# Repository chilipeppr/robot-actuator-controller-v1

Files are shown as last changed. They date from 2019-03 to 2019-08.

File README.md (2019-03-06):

# robot-actuator-controller-v1
This is a controller for the WE-R2.4 robot on Thingiverse.

It has an ESP32 at the heart of the controller to enable control of the actuator via Wifi or Bluetooth. There is a DC to DC converter to step down the 24v driving the DRV8825 stepper motor driver to 5V for powering the ESP32. The DRV8825 has all ports connected into the ESP32 to send step and direction pulses for control of the stepper motor.

There is also a WS2812 LED connected for indicating status of the controller.

A switch has been added for when you're using the USB port for programming the ESP32. You need to switch off the 5V from the DC to DC converter to connect USB from your computer.

The wrist cap has been extended from Jeff Kerr's original design to fit this larger board.

# Eagle Board and Schematic

The .brd and .sch files are Eagle board and schematic files. You can download Eagle for free to view or edit the boards or just use the .zip file in the "pcb fabricator" folder to send to your board house like JLCPCB where it only costs $2 to get your boards made.

# ESP32 Firmware

You need to upload the firmware in this repo to your ESP32 using esptool.py which is available on the Espressif website. There's also a video on http://chilipeppr.com/esp32 on how to use the workspace. This video shows you how to upload the firmware and use the workspace to upload code.

To program your board with this firmware use the command on Windows:
esptool.py --port COM5 write_flash 0x1000 bootloader.bin 0x10000 NodeMCU.bin 0x8000 partitions.bin

You need to install esptool.py via Python's package manager or from downloading direct from Espressif's website.

An alternate path is to use the esp32tool.zip I provide in the workspace and swap out the NodeMCU.bin file in this repo to the one in that zip file. Then install. You do need 3 .bin files to program the firmware. 2 of them are standard (bootloader.bina nd partitions.bin), but the NodeMCU.bin is the new file you'd have to swap in.

This firmware is configured for 230,400 baud, so don't forget to change to that value in ChiliPeppr when you connect to the board. If you try the default 115,200 it will fail.

# CAD Design Fusion 360

The CAD design of the extended wrist cap with the electronics inside is available at https://gallery.autodesk.com/fusion360/projects/robot-arm-esp32-drv8825-actuator-controller

# How to Upload the Lua Code

The ChiliPeppr ESP32 for Lua Workspace was used to program the board and is available at http://chilipeppr.com/esp32

Video on how to use the ESP32 for Lua workspace to upload firmware and Lua code on your ESP32. https://www.youtube.com/watch?v=njAeHfoVIoY

# Thingiverse

Jeff Kerr's (LoboCNC) original 3D printed robot arm design is on Thingiverse at https://www.thingiverse.com/thing:3327968/

# PCB Components

ESP32 Wemos $8 (Many ESP32 devices are cheaper, but this is the smallest size broadly available to fit inside the small actuators)
https://www.aliexpress.com/item/ESP32-wemos-ESP32-WiFi-Modules-Bluetooth-Dual-ESP-32-ESP-32S-ESP8266/32815190965.html

DRV8825 Stepper Board $0.95
https://www.aliexpress.com/item/5pcs-lot-3D-Printer-Stepstick-Drv8825-Stepper-Motor-Driver-Reprap-4-PCB-Board-Free-shipping-replace/32514641632.html

DC to DC Converter $0.90 (Pick the 5V version, not 3.3V)
https://www.aliexpress.com/item/DC-DC-Power-Supply-Module-Step-Down-3A-output-24V-12V-to-5V-3-3V-Buck/32904709711.html

WS2812B LED $0.15 per (Choose white and WS2812B)
https://www.aliexpress.com/item/10-1000pcs-4-Pin-WS2812B-WS2812-LED-Chip-Heatsink-5V-5050-RGB-WS2811-IC-Built-in/32634454437.html

Slide Switch $0.29 for 20 pieces
https://www.aliexpress.com/item/20Pcs-Interruptor-on-off-mini-Slide-Switch-SS12D00-SS12D00G3-3pin-1P2T-2-Position-High-quality-toggle/32964400942.html

Screw Terminal
https://www.aliexpress.com/item/20-pcs-2-Pin-Screw-blue-green-PCB-Terminal-Block-Connector-5mm-Pitch/32814618602.html

26AWG Silicone Ultra Flexible Wire for 24v (Use 2 of the 4 wires)
https://www.aliexpress.com/item/2metre-26AWG-28AWG-30AWG-Silicone-Wire-Ultra-Flexiable-Test-Line-3P-4P-6P-0-08mm-Tinned/32870367030.html

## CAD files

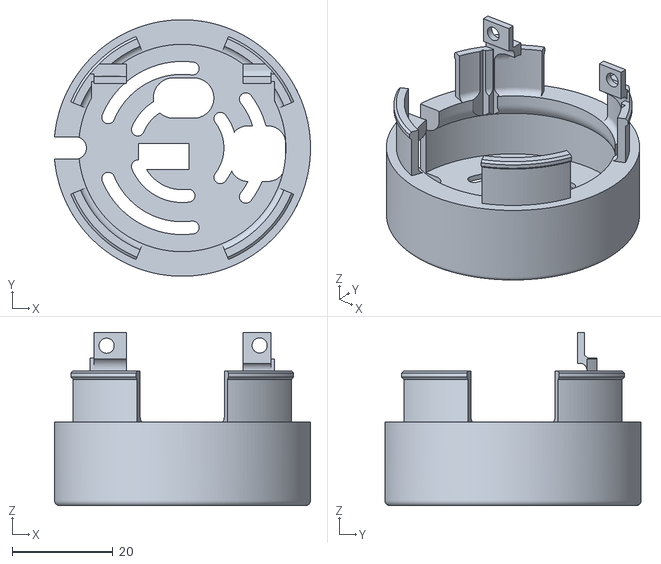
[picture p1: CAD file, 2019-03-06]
stl file for 3d printing/wrist shell cap.stl
50.7 x 50.8 x 34.3

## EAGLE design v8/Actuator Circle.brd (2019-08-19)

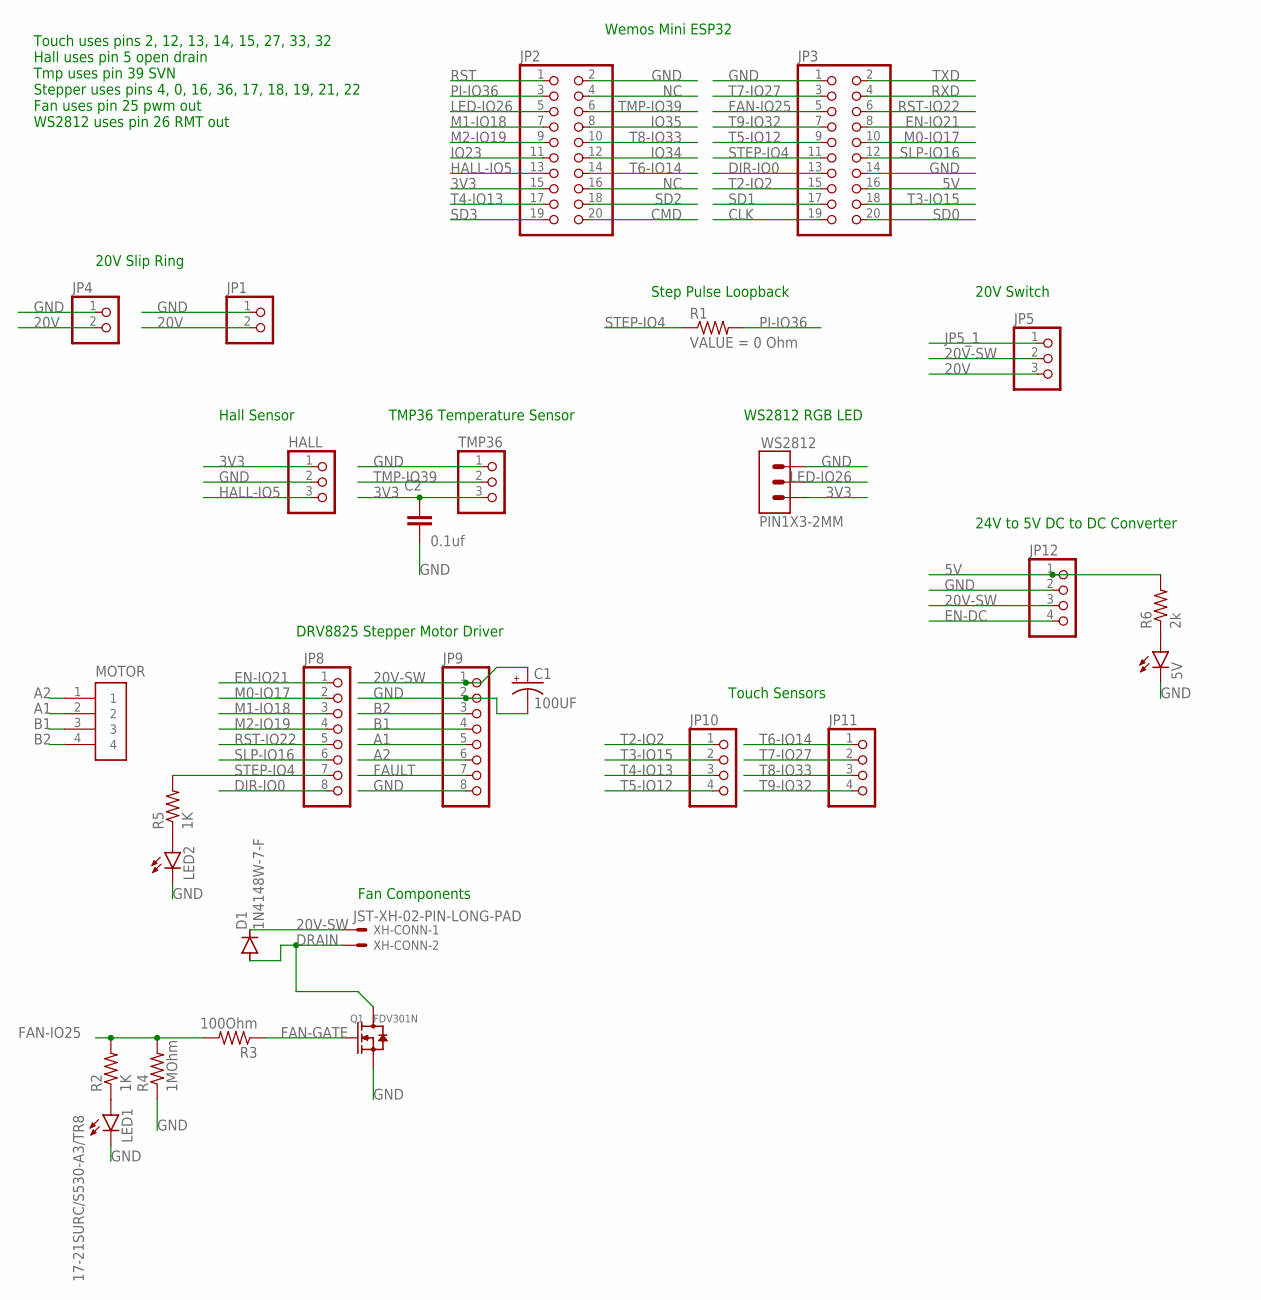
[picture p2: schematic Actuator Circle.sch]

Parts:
5V: 17-21SURC/S530-A3/TR8; CHIPLED_0805
C1: 100UF; E2,5-6
C2: 0.1uf; CAP_0603
D1: 1N4148W-7-F; SOD123
HALL: PINHD-1X3; 1X03
JP1, JP4: PINHD-1X2; 1X02
JP2, JP3: PINHD-2X10; 2X10
JP5: PINHD-1X3/90; 1X03/90
JP8, JP9: PINHD-1X8; 1X08
JP10, JP11, JP12: PINHD-1X4; 1X04
LED1, LED2: 17-21SURC/S530-A3/TR8; CHIPLED_0805
MOTOR: B4B-PH-K-S(LF)(SN); JST_B4B-PH-K-S(LF)(SN)
Q1: FDV301N; SOT23
R1: 0 Ohm; RES_0402
R2, R5: 1K; RES_0402
R3: 100Ohm; RES_0402
R4: 1MOhm; RES_0402
R6: 2k; RES_0402
TMP36: PINHD-1X3; 1X03
WS2812: PIN1X3-2MM
XH-CONN: JST-XH-02-PIN-LONG-PAD; JST-XH-02-PACKAGE-LONG-PAD

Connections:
3V3: C2.1, HALL.1, JP2.15, TMP36.3, WS2812.3
5V: JP3.16, JP12.1, R6.2
20V: JP1.2, JP4.2, JP5.3
20V-SW: C1.+, D1.1 (C), JP5.2, JP9.1, JP12.3, XH-CONN.1
A1: JP9.5, MOTOR.2
A2: JP9.6, MOTOR.1
B1: JP9.4, MOTOR.3
B2: JP9.3, MOTOR.4
CLK: JP3.19
CMD: JP2.20
DIR-IO0: JP3.13, JP8.8
DRAIN: D1.2 (A), Q1.3 (D), XH-CONN.2
EN-DC: JP12.4
EN-IO21: JP3.8, JP8.1
FAN-GATE: Q1.1 (G), R3.1
FAN-IO25: JP3.5, R2.2, R3.2, R4.2
FAULT: JP9.7
GND: 5V.C, C1.-, C2.2, HALL.2, JP1.1, JP2.2, JP3.1, JP3.14, JP4.1, JP9.2, JP9.8, JP12.2, LED1.C, LED2.C, Q1.2 (S), R4.1, TMP36.1, WS2812.1
HALL-IO5: HALL.3, JP2.13
IO23: JP2.11
IO34: JP2.12
IO35: JP2.8
JP5_1: JP5.1
LED-IO26: JP2.5, WS2812.2
M0-IO17: JP3.10, JP8.2
M1-IO18: JP2.7, JP8.3
M2-IO19: JP2.9, JP8.4
unnamed: LED1.A, R2.1
unnamed: LED2.A, R5.1
unnamed: 5V.A, R6.1
NC: JP2.4, JP2.16
PI-IO36: JP2.3, R1.2
RST: JP2.1
RST-IO22: JP3.6, JP8.5
RXD: JP3.4
SD0: JP3.20
SD1: JP3.17
SD2: JP2.18
SD3: JP2.19
SLP-IO16: JP3.12, JP8.6
STEP-IO4: JP3.11, JP8.7, R1.1, R5.2
T2-IO2: JP3.15, JP10.1
T3-IO15: JP3.18, JP10.2
T4-IO13: JP2.17, JP10.3
T5-IO12: JP3.9, JP10.4
T6-IO14: JP2.14, JP11.1
T7-IO27: JP3.3, JP11.2
T8-IO33: JP2.10, JP11.3
T9-IO32: JP3.7, JP11.4
TMP-IO39: JP2.6, TMP36.2
TXD: JP3.2

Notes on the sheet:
Touch Sensors
DRV8825 Stepper Motor Driver
Wemos Mini ESP32
Fan Components
24V to 5V DC to DC Converter
20V Slip Ring
Hall Sensor
TMP36 Temperature Sensor
WS2812 RGB LED
Touch uses pins 2, 12, 13, 14, 15, 27, 33, 32 Hall uses pin 5 open drain Tmp uses pin 39 SVN Stepper uses pins 4, 0, 16, 36, 17, 18, 19, 21, 22 Fan uses pin 25 pwm out WS2812 uses pin 26 RMT out
Step Pulse Loopback
20V Switch

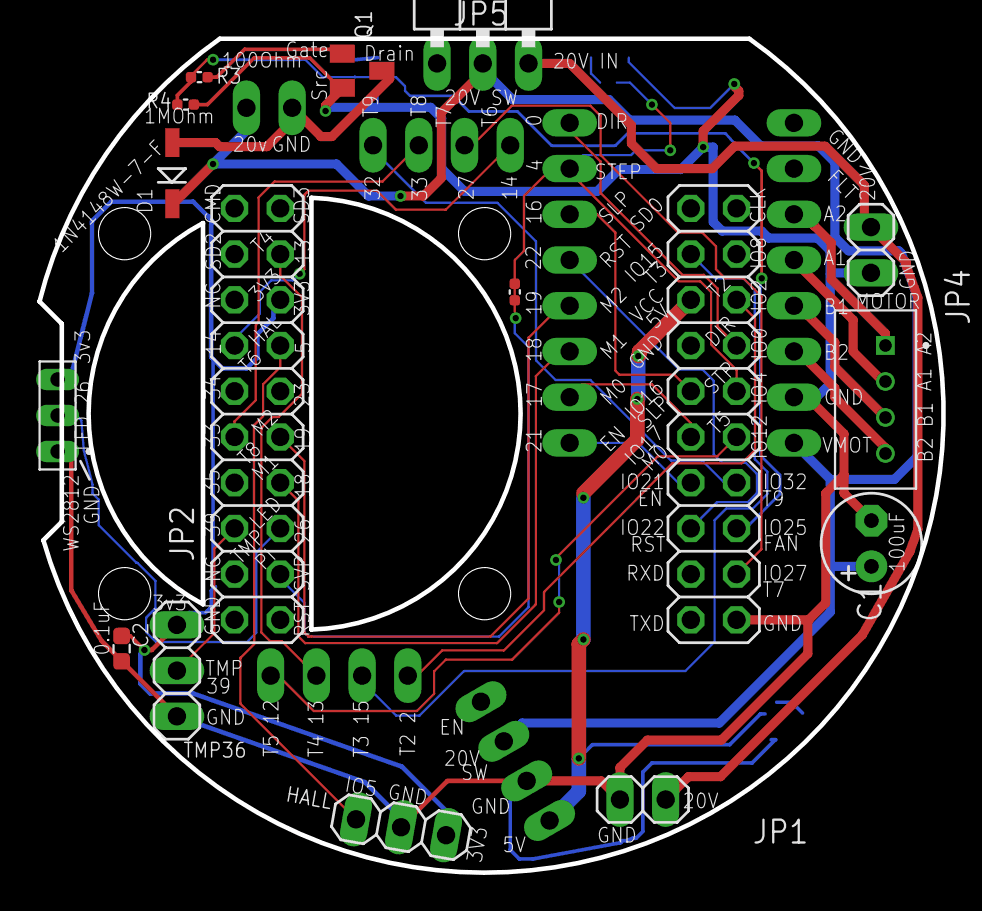
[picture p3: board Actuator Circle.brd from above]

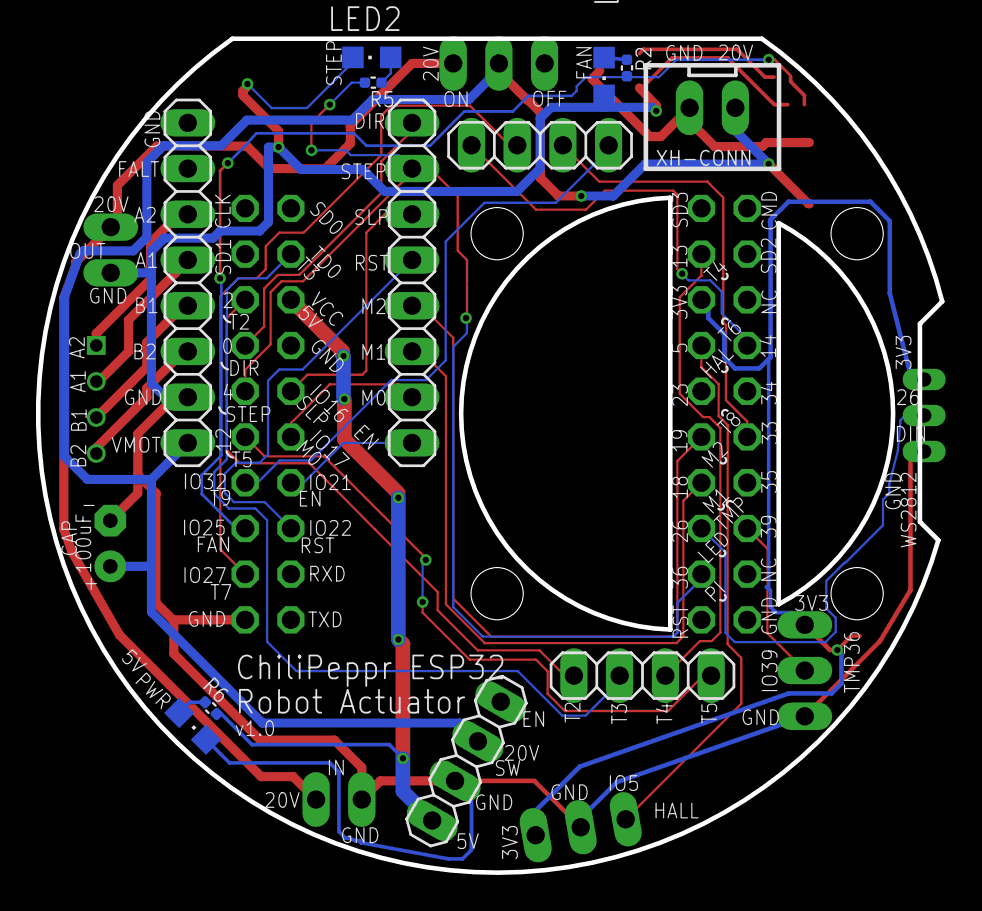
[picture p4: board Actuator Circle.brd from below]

Board: 2 copper layers, 50.2 x 46.3 mm, 28 parts (12 on the bottom side), 36 nets.

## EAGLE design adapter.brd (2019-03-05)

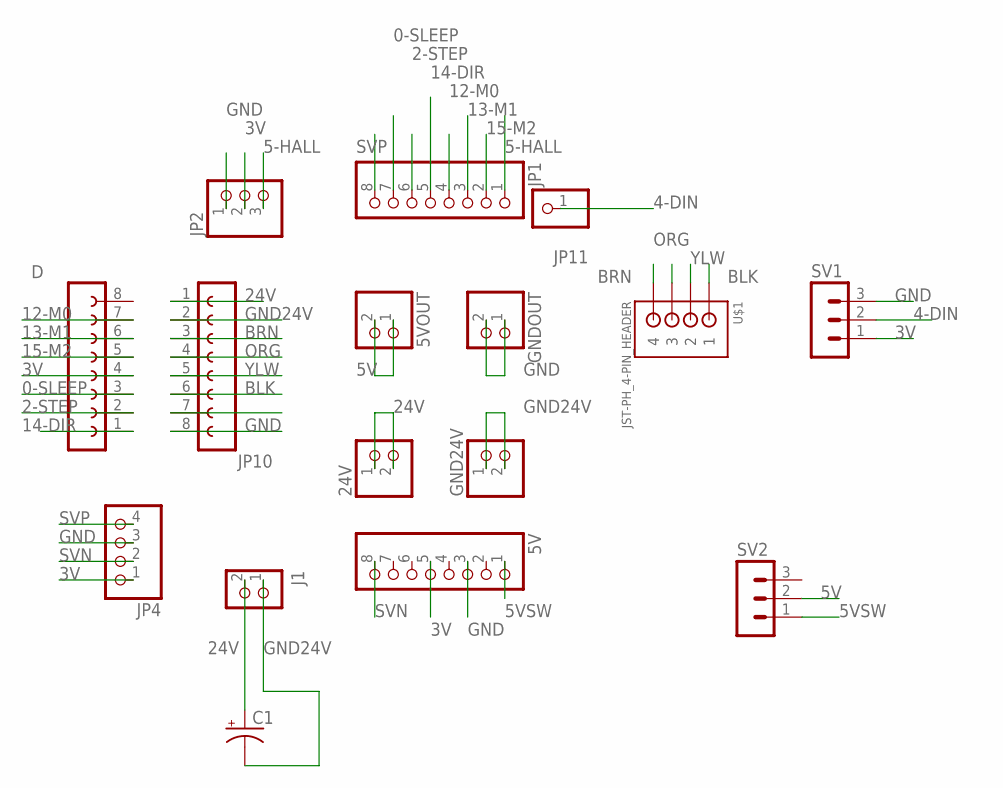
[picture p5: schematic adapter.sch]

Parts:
5V: PINHD-1X8; 1X08
5VOUT, 24V: PINHD-1X2; 1X02
C1: CPOL-USE5-6; E5-6
D: FE08-1; FE08
GND24V: PINHD-1X2; 1X02
GNDOUT: PINHD-1X2; 1X02
J1: CON_TERMINAL_BLOCK_02-5MM; TERMINAL_BLOCK_2P_5
JP1: PINHD-1X8; 1X08
JP2: PINHD-1X3; 1X03
JP4: PINHD-1X4; 1X04
JP10: FE08-1; FE08
JP11: PINHD-1X1; 1X01
SV1, SV2: MA03-1
U$1: JST-PH_4-PIN_HEADER; JST_B4B-PH_HEADER

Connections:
0-SLEEP: D.3, JP1.7
2-STEP: D.2, JP1.6
3V: 5V.5, D.4, JP2.2, JP4.1, SV1.1
4-DIN: JP11.1, SV1.2
5-HALL: JP1.1, JP2.3
5V: 5VOUT.1, 5VOUT.2, SV2.2
5VSW: 5V.1, SV2.1
12-M0: D.7, JP1.4
13-M1: D.6, JP1.3
14-DIR: D.1, JP1.5
15-M2: D.5, JP1.2
24V: 24V.1, 24V.2, C1.+, J1.2, JP10.1
BLK: JP10.6, U$1.P1 (1)
BRN: JP10.3, U$1.P4 (4)
GND: 5V.3, GNDOUT.1, GNDOUT.2, JP2.1, JP4.3, JP10.8, SV1.3
GND24V: C1.-, GND24V.1, GND24V.2, J1.1, JP10.2
ORG: JP10.4, U$1.P3 (3)
SVN: 5V.8, JP4.2
SVP: JP1.8, JP4.4
YLW: JP10.5, U$1.P2 (2)

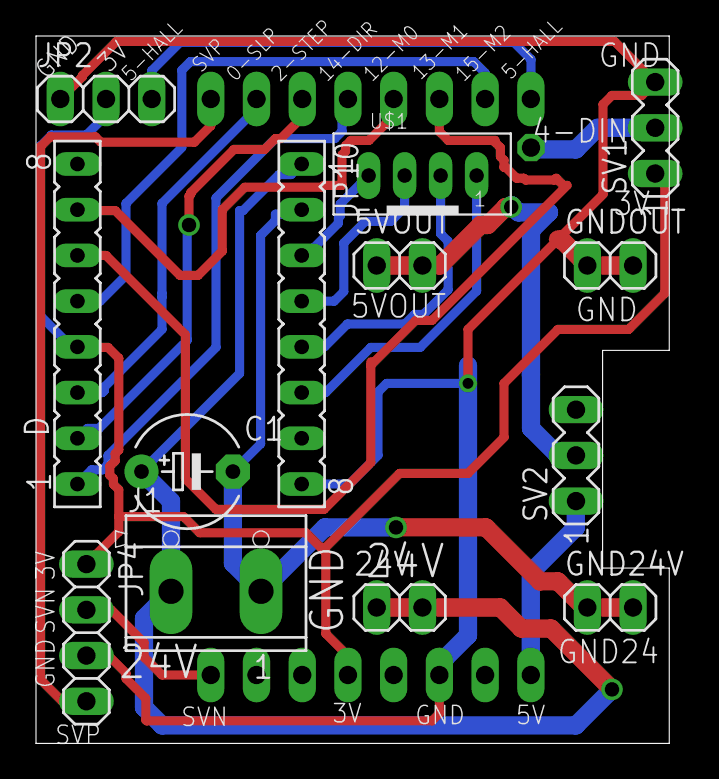
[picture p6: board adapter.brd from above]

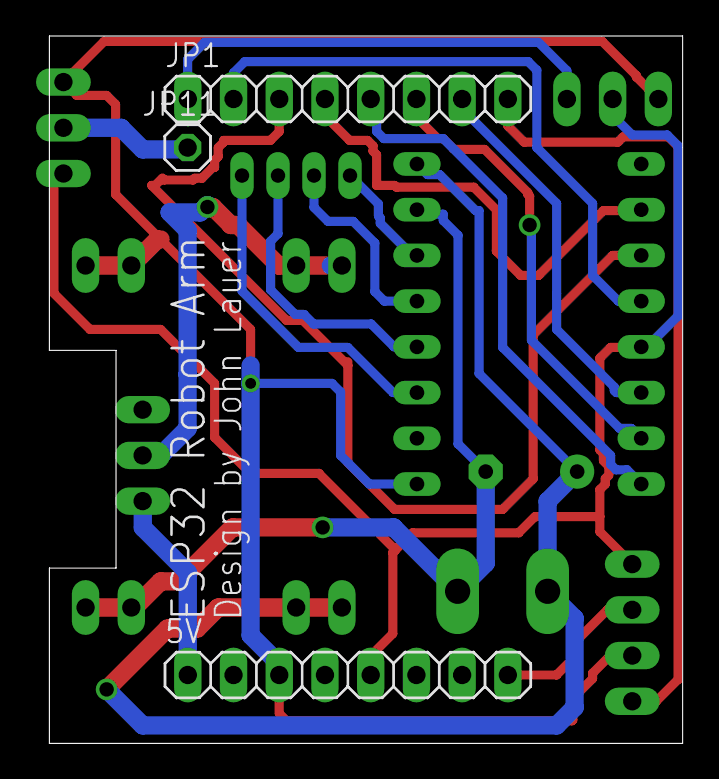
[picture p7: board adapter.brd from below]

Board: 2 copper layers, 35.2 x 39.3 mm, 16 parts (3 on the bottom side), 20 nets.

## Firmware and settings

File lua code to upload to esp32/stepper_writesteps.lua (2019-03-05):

Stepper = {}

-- Stepper.pinReset = 5
Stepper.pinSleep = 0 --15
Stepper.pinStep = 2 --13
Stepper.pinDir = 14 --12
Stepper.pinM0 = 12
Stepper.pinM1 = 13
Stepper.pinM2 = 15

function Stepper.init()
  gpio.config({
    gpio= {
      Stepper.pinSleep, Stepper.pinStep, Stepper.pinDir,
      Stepper.pinM0, Stepper.pinM1, Stepper.pinM2
    },
    dir=gpio.OUT,
  })
  -- gpio.write(Stepper.pinReset, 1)
  gpio.write(Stepper.pinSleep, 1)
  gpio.write(Stepper.pinStep, 1)
  gpio.write(Stepper.pinDir, 1)
  gpio.write(Stepper.pinM0, 1)
  gpio.write(Stepper.pinM1, 1)
  gpio.write(Stepper.pinM2, 1)
end

function Stepper.test()
  for i=400,50,-2 do
    -- print(i)
    stepper.writeSteps( {pin=Stepper.pinStep, steps=4, dur=i } ); 
  end
  stepper.writeSteps( {pin=Stepper.pinStep, steps=200*32*1, dur=100 } ); 
  for i=50,400,2 do
    -- print(i)
    stepper.writeSteps( {pin=Stepper.pinStep, steps=4, dur=i } ); 
  end
  
  -- print("done")
  -- stepper.write({pin=12, dur=10000, data=string.char(0xAA)})
  print("did stepper write")
end

function Stepper.sleep()
  gpio.write(Stepper.pinSleep, 0)
end

function Stepper.wake()
  gpio.write(Stepper.pinSleep, 1)
end

Stepper.tmr = null
function Stepper.loop()
  Stepper.wake()
  Stepper.tmr = tmr.create()
  Stepper.tmr:alarm(2000, tmr.ALARM_SEMI, function()
    Stepper.toggleDir()
    Stepper.wake()
    Stepper.test()
    Stepper.sleep()
    Stepper.tmr:start()
  end)
end 

function Stepper.stop()
  Stepper.tmr:stop()
  Stepper.tmr:unregister()
end

Stepper.lastDir = 1
function Stepper.toggleDir()
  if Stepper.lastDir == 0 then
    Stepper.lastDir = 1
  else
    Stepper.lastDir = 0
  end
  gpio.write(Stepper.pinDir, Stepper.lastDir)
end

Stepper.init()
-- Stepper.test()
Stepper.loop()

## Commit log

2019-03-05 Send this zip to board fabricator
2019-03-06 Create wrist shell cap.stl
    [wrist shell cap.stl]
2019-03-22 Fixed the correct PCB
2019-08-19 v8 update
    [Actuator Circle.brd, Actuator Circle.sch, Touch.brd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]
